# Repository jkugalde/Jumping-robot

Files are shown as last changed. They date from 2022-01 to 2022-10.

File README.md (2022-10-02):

# Jumping Robot

I used 2 [N20 Servo Modules](https://github.com/jkugalde/N20-Servo-Module) to make a jumping five bar parallel robot. 

## Summary

I printed a mechanical linkage to make a 5 bar mechanism using the modules. The assembly instructions are [HERE](INSTRUCTIONS.md).

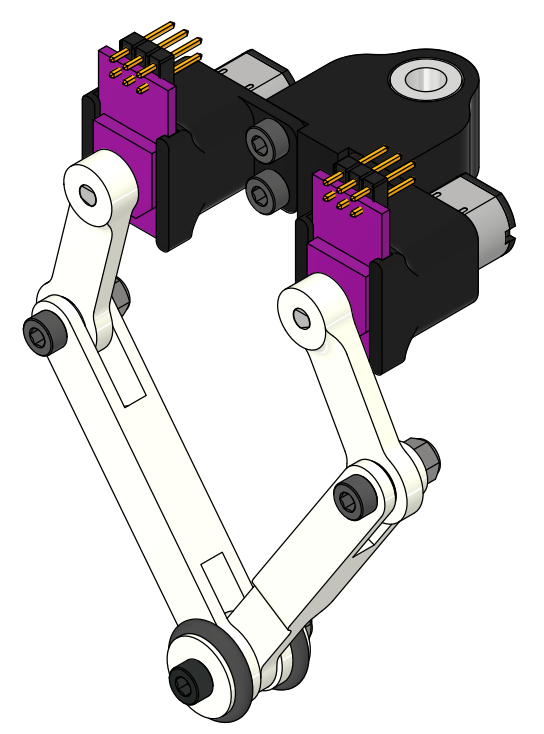
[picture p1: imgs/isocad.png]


## First experiments

With the 3000 RPM (1:10 gearbox) motor, the robot barely jumps at a voltage (9V) higher than the nominal (6V), which can be damaging it. A motor with at least twice the torque should be enough to have a better performance without losing too much speed, but further calculations are needed.

Currently, i have made some Arduino libraries to play with the leg, and it can jump as you can see in this [video](https://youtu.be/bBeYL-RNnhY). 

## Further Work

- To use a Teensy instead of an Arduino.
- Write direct and inverse kynematics.
- Make a PCB.
- Add some compliancy.

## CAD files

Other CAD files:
CADfiles/Brushed DC Motor v8.iam
CADfiles/LegLinksAssembly.iam
CADfiles/LinkA SB.ipt
CADfiles/LinkB SB.ipt
CADfiles/PotHolder.ipt

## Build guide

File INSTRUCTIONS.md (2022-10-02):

# Hardware

The parts are stored [HERE](https://grabcad.com/library/jumping-robot-leg-1).

The middle joint is designed in this case to hold a 5 mm DI spacer to act as a bushing in the jumping setup, which is a fixed pole.



## Commercial parts

This is the commercial parts list to make a working leg (2 modules), the rest is 3d printing. See the module [repository](https://github.com/jkugalde/N20-Servo-Module) to make 2 modules. 

 ITEM              | QTY
 ---------------------------   | ------------
 M3x18 socket bolt | 1
 M3x12 socket bolt | 2
 M3x6 socket bolt | 4
 M3 Locknut | 3
 Bearing 683ZZ | 3
 Oring 11 DI 2.5 mm t | 2
 Arduino (any Arduino) | 1 
 DRV8801 motor driver | 2

 You also need a power source capable of providing at least 9V at 3A, maybe a 2S LiPo battery. I'm using that motor driver to use the current measurement in the future, but you can use a L298N if you want to do only position control. I did not include the 5 mm aluminium spacer, as you may use another thing in your jumping experimental setup. A dual control driver should be a good idea for the legs, instead of a single driver per motor.

 ## 3D printed parts

 This is the printed parts list:

  ITEM              | QTY
 ---------------------------   | ------------
 Motor joint link | 2
 Link A | 1
 Link B | 1
 Rubber support | 2
 Middle joint | 1

 The parts are printed using a FDM printer. I used PETG as the motor can get hot and weaken the press fit between the motor and the parts. 

 ## Assembly

### Leg

- Once you have 2 modules, joint them together using the middle joint and the M3x6 bolts. The holes in the printed part are smaller than the bolts, so a thread is made.
- Put a bearing inside each hole in the links.
- Join links A and B.
- Put a rubber support in each side.
- Bolt the joint using the M3x18 bolt and locknut. 
- Put the orings in their place.
- Join the links A-B with the motor joint links and the M3x12 bolts.
- Press fit the mechanism in the motor shafts.

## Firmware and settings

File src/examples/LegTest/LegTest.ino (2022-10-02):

#include "RobotLeg.h"

const int pinsA[4] = {2,3,A0,4}; // dir, pwm, sensor in, sleep. 
const int pinsB[4] = {8,9,A1,10};

const float kA[3] = {4,0.2,0}; // PID values, kp, kd, ki
const float kB[3] = {4,0.2,0};

const int refsA[2] = {785,530}; //analog reference for angle 0 and 90 (from the horizontal)
const int refsB[2] = {770,500};

const float leglengths[5]={25.0,50.0,25.0,50.0,56.3};
RobotLeg RL1(leglengths); //creates the leg

int newpos1=45; //initial angles
int newpos2=45;

const int leg_pwm=255; //max power in actuator

int count=0; //index
int cual = 0;
const int nmoves = 2; //quantity of preprogrammed moves

const int q1[nmoves]={140,90}; // pre programmed moves
//const int q2[nmoves]={74,72,70,60,50,35,32,30,32,50,60,70,72,74};

unsigned long timer = 0;
unsigned long dt = 400; //time between each movement

void setup() {

  Serial.begin(9600);
  RL1.motorpins(pinsA,pinsB); //assign pns
  RL1.setks(kA,kB); //assign pid constants
  RL1.setrefs(refsA,refsB); //assign references
  RL1.dirs(false,true);
  timer=millis(); //set timer

RL1.goTo(newpos1,newpos2,leg_pwm); //initial position

delay(2000); //wait
  
}

void loop() {

if(millis()-timer>=dt){  //this sweeps the arrays

  newpos1=q1[count];
  newpos2=180-newpos1;
  count=count+1;
  if(count==nmoves){
  count=0;
  }
  timer=millis();
}

// if(Serial.available()>0){
// if(cual==0){

// newpos1=Serial.parseInt();
// cual=cual+1;
// }
// else{
// newpos2=Serial.parseInt();
// RL1.ik(newpos1,newpos2,255);
// cual=0;  
// }
// }

RL1.goTo(newpos1,newpos2,leg_pwm);
  
}

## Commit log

2021-11-28 smaller chasis, libraries and examples
    [623zz.iam, 683ZZ_Bearing.STEP, Base.0004.ipt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]
2021-11-29 ajuste de tolerancias, funciones de calibracion
    [Leg Assembly (small bearing).0020.iam, Leg Assembly (small bearing).0021.iam, Leg Assembly (small bearing).iam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]
2021-12-01 driver change
2021-12-10 new modular design
    [5pinheader.ipt, 683zz.ipt, Base.ipt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]
2021-12-10 tolerance adjustment
    [Case.0016.ipt, Case.ipt, Couple.0005.ipt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]
2021-12-27 new module design
    [Brushed DC Motor v8.0006.iam, Brushed DC Motor v8.0007.iam, Brushed DC Motor v8.iam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]
2022-01-05 final design
    [2x3pinheader.0001.iam, 2x3pinheader.iam, 5pinheader.ipt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]
2022-09-16 Commited files efore removing them
    [2x3pinheader.0001.iam, LegAssembly.0012.iam, LegAssembly.iam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]
2022-09-16 Deleted all CADfiles files
    [2x3pinheader.iam, 6-Pin Header-Male-Double-2.54mm.ipt, 683zz.ipt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]
2022-09-16 assembly instructions, commented code
